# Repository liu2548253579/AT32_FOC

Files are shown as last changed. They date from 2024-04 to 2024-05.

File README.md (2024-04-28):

# AT32_FOC

## 介绍

此项目使用AT32主控驱动两路无刷电机，板载陀螺仪mpu6050，外置EEPROM，OLED屏幕，CAN口，两路AS5600磁编码器，旨在使用极低成本实现对无刷电机实现FOC控制，并且大部分元器件采用国产品牌，此板可用于无刷电机驱动，也可做为小平横车，预留串口和SWD调试接口方便后续外接其他设备。

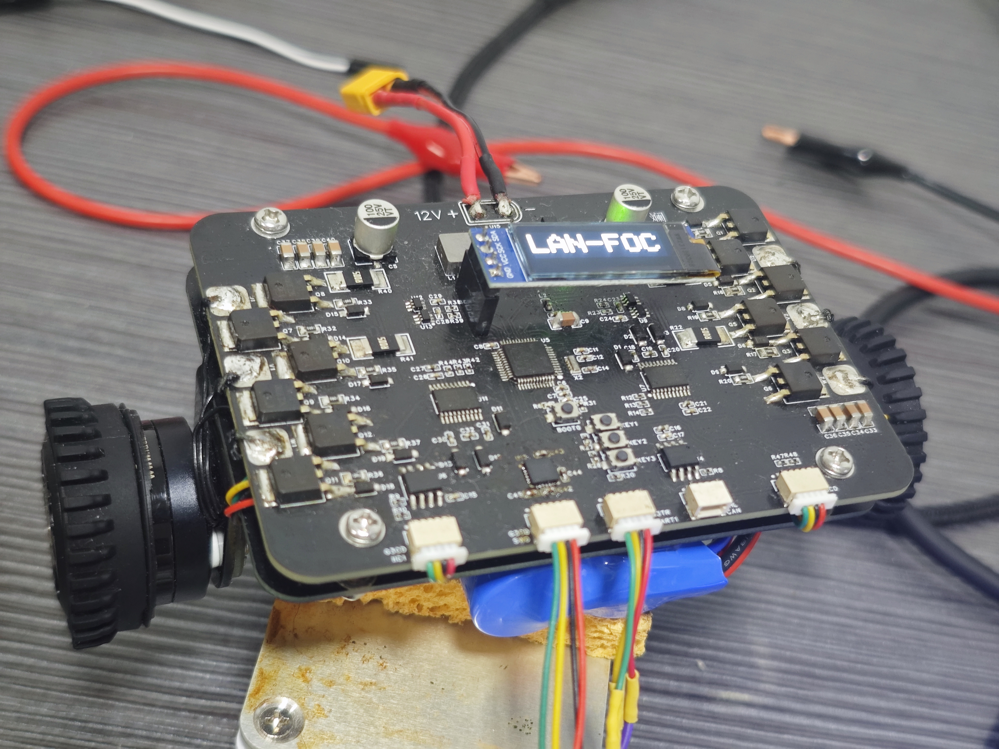
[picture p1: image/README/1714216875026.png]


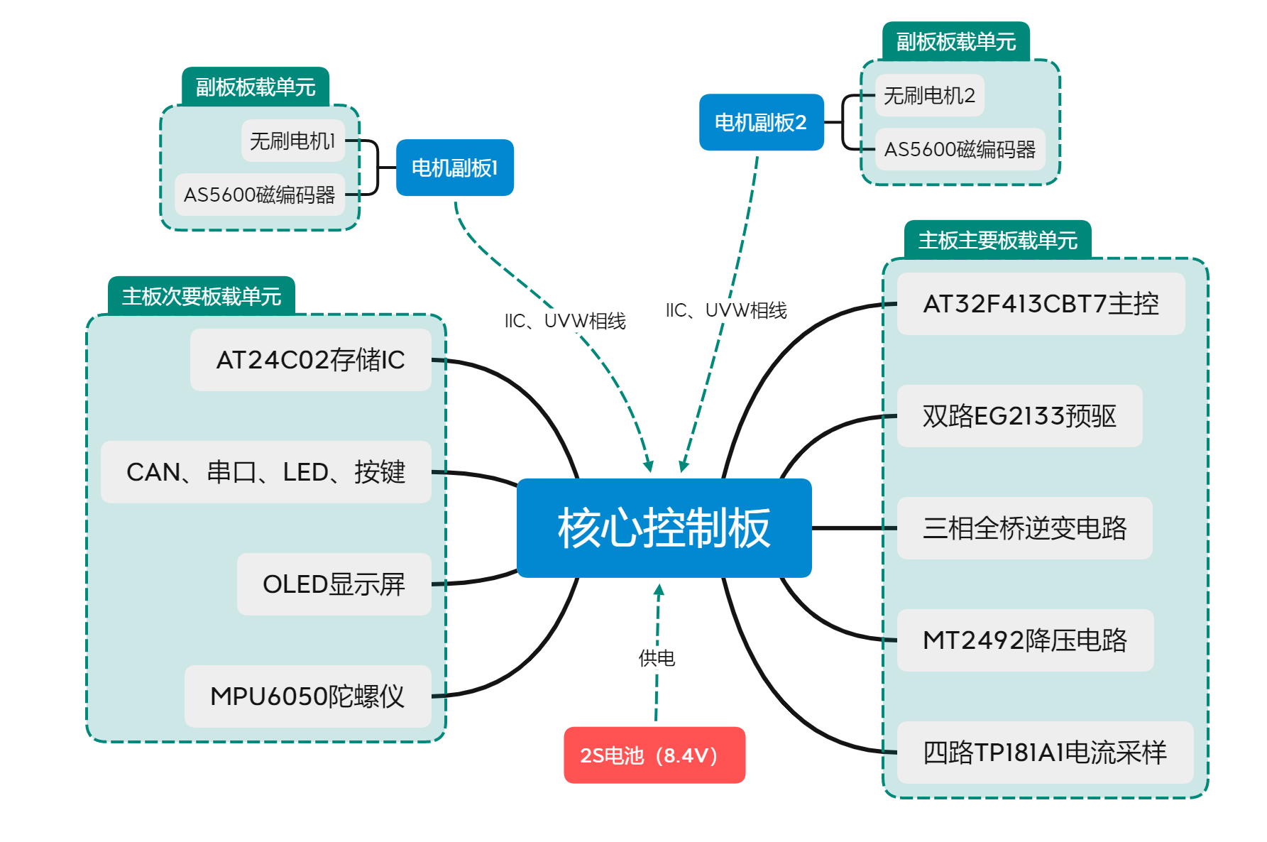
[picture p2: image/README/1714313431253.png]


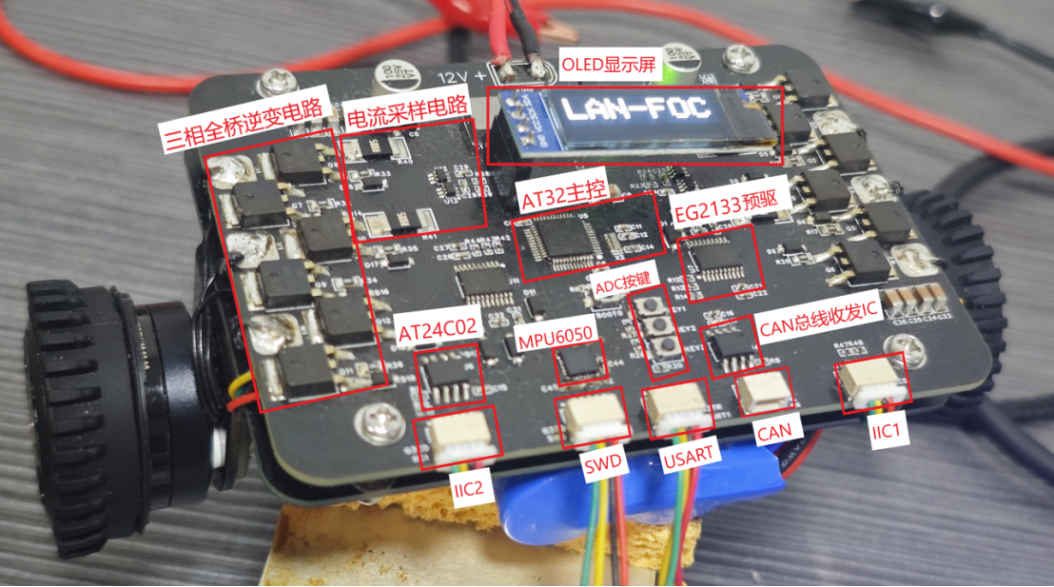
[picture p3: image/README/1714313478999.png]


## 一、硬件设置

请跟据hardware文件夹中的PCB文件打样PCB并将元器件贴装好，编码器底板适配带有径向磁铁的无刷电机

板子供电最大支持12V，但是我建议使用2S电池供电，也就是最大8.4V

无刷电机使用2210云台电机（110kV，6PP），但对于这个板子的MOS驱动能力来说完全是吕布骑狗了

预驱使用EG2133非常便宜，MOS使用NCE3080K足以应对绝大部分无刷电机

电流采样电阻为5毫欧的合金采样电阻，使用TP181A1-CR作为电流检测IC增益为50

MCU使用AT32F413CBT7

## 二、软件配置

软件使用platformio开发stm32程序基于Arduino框架，套用st官方维护的SDK，但是由于AT32和STM32的寄存器地址有部分不同，所以官方的SDK被我魔改过，在打开软件工程等待Platformio配置好环境之后，将此压缩包解压到你的platformio的package目录，这样我的修改就会生效，或者你如果不嫌麻烦或者想使用其他版本的SDK，可以根据我这两篇文章来自行配置：

[Arduino如何添加没有适配的GPIO](https://zhuanlan.zhihu.com/p/693456340)

[Arduino如何设置未适配的IO作为功能引脚](https://zhuanlan.zhihu.com/p/693467202)

在一切配置完毕之后你就可以烧录使用了，但注意我在ini配置中制定了烧录器为jlink如果你没有jlink请修改为其他方式

## 三、待完成事项

* [X] 完成AT32时钟适配
* [X] 完成ADC、PWM、UART、IIC、LED、KEY配置
* [X] 完成MPU6050、OLED、EEPROM、CAN配置
* [X] 实现无刷电机开环控制
* [X] 实现无刷电机角度闭环与速度闭环控制
* [X] 为无刷电机添加电流环
* [ ] 添加几个电机互动小功能
* [ ] 设计电池电压检测保护电池
* [ ] 设计多功能菜单调节参数
* [ ] 设计CAN协议实现参数在线查看与配置
* [ ] 调节PID使其可以直立并控制

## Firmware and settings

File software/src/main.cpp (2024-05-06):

#include "at32_config.h"
#include "foc_config.h"
#include "peripherals_config.h"
#include "menu.h"
#include "motion.h"
#include "interrupt.h"

#define protect_voltage 6.7f



void setup() {
  at32_board_init(); //CLOCK IO UART IIC initialization
  peripherals_init();//MPU6050 SSD1306 AT24C02

  Menu_Show_3("LOW-VOL");
  Get_Initial_Voltage(&sensor_data,protect_voltage);//6.7V initial voltage
  // eeprom.update(0x80,0x02);
  // Serial.println("data------------------------------");
  // Serial.println(eeprom.read(0x80));
  // Serial.println("data------------------------------");

  Menu_Show_3("HOLD-ON");
  mpu6050.calcGyroOffsets(false);


  // I2C1_EV_IRQn
  Menu_Show_3("LAN-FOC");
  foc_init(sensor_data.Bat_val_init);        //FOC initialization

  // bool ret = CANInit(CAN_500KBPS, 2);  // CAN_RX mapped to PB8, CAN_TX mapped to PB9
  // if (!ret) while(true);

  Menu_Show_3("INIT-OK");
  Serial.printf("INIT_OK\r\n");

  timer_init();//定时器初始化
}


void FOC_Loop(bool enable)
{
  runFOC();
  if(enable)
  {
    switch (main_menu.mode)
    {
    case 1:
      Motion_Set_Velocity_Both(Rpm_to_Rad(main_menu.Velocity));
      break;
    case 2:
      Motion_Sync();
      break;
    case 3:
      Motion_Set_Angle_Both(Angle_to_Rad(main_menu.Angle));
      break;
    case 4:
      Close_Output();
      Clear_FOC_Data();
      break;
    case 5:
      Close_Output();
      Clear_FOC_Data();
      break;

    default:
      break;
    }


  }




}



void loop() {


    if(time_1ms>=1)
    {
      time_1ms=0;
      FOC_Loop(main_menu.Enable);
    }
    

    if(time_10ms>=10)//10ms执行一次
    {
      time_10ms=0;
      Get_Mpu6050_Data(&sensor_data);
      Get_Foc_Data(&sensor_data);
      if(main_menu.Enable)
      {
        if(main_menu.mode==0)//Banlance
        {
          float out0,out1,out_velocity,out_velocity1;

          out_velocity=Motion_Balance_Velocity(sensor_data.Velocity_val,0.0f);
          out_velocity1=Motion_Balance_Velocity(sensor_data.Velocity_val1,0.0f);          
          out0=Motion_Balance_Angle(&sensor_data,out_velocity);
          out1=Motion_Balance_Angle(&sensor_data,out_velocity1);

          Banlance_Set_Velocity(0,out0);
          Banlance_Set_Velocity(1,out1);  
        }
        else
        {
          Serial_Print_All_Data(&sensor_data);
        }

      }
    }

    if(time_200ms>=200)//200ms执行一次
    {
      time_200ms=0;
      Get_Analog_Data(&sensor_data);
      ShowMenu(&main_menu);
      digitalToggleFast(LED_PIN);

      if(!main_menu.Enable)
      {
        Clear_FOC_Data();
        Close_Output();
      }

      if(sensor_data.Bat_val<protect_voltage)//低电量关闭输出
      {
        main_menu.Enable=0;
        Menu_Show_3("LOW-VOL");//显示低电量
        Close_Output();
      }
      if(sensor_data.Key_val==3)//确定键
      {
        sensor_data.Key_val=0;
        main_menu.Enable=!main_menu.Enable;
      }


      if(!main_menu.Enable)//主界面菜单
      {
        if(sensor_data.Key_val==1){sensor_data.Key_val=0;main_menu.mode--;}
        if(sensor_data.Key_val==2){sensor_data.Key_val=0;main_menu.mode++;}
      }
      else//功能界面
      {
        if(main_menu.mode==1)
        {
          if(sensor_data.Key_val==1){sensor_data.Key_val=0;main_menu.Velocity+=50;}
          if(sensor_data.Key_val==2){sensor_data.Key_val=0;main_menu.Velocity-=50;}
          if(main_menu.Velocity<=-500){main_menu.Velocity=-500;}
          if(main_menu.Velocity>=500){main_menu.Velocity=500;}
        }
        if(main_menu.mode==3)
        {
          if(sensor_data.Key_val==1){sensor_data.Key_val=0;main_menu.Angle+=30;}
          if(sensor_data.Key_val==2){sensor_data.Key_val=0;main_menu.Angle-=30;}
        }
      }


    }
}

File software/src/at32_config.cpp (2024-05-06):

#include "at32_config.h"
#include "math.h"

/*
线阻15欧姆
波特率115200

LED(PB1)
按键ADC(PA0)
电池ADC(PB0)

MOTOR1(PA8 PA9 PA10)
AS5600_1(PF6-SCL PF7-SDA)Wire1
I-SENSE1(PA6 PA7)

MOTOR2(PA1 PA2 PA3)
AS5600_2(PB10-SCL PB11-SDA)Wire
I-SENSE2(PA4 PA5)

MPU6050(PF6-SCL PF7-SDA)Wire1
FLASH(PF6-SCL PF7-SDA)Wire1
OLED(PB10-SCL PB11-SDA)Wire

SWD(PA13-CLK PA14-DIO)
USART1(PB6-TX PB7-RX)
CAN(PB8-RX PB9-TX)
*/

TwoWire Wire1 = TwoWire(); //D14-D15



void at32_i2c_clock_config(void)
{
__HAL_RCC_I2C1_CLK_ENABLE();
__HAL_RCC_AFIO_CLK_ENABLE();
__HAL_RCC_I2C1_REMAP_CLK_ENABLE();
__HAL_RCC_GPIOF_CLK_ENABLE();
}



void gpio_pin_remap_config(uint32_t gpio_remap, confirm_state new_state)
{
    uint32_t reg_addr, remap_mask;
    uint8_t bit_offset, bit_num, bit_val;

    /* get register address, bit offset, bit number and remap value */
    reg_addr = IOMUX_BASE + (gpio_remap >> 24);
    bit_offset = (gpio_remap >> 16) & 0xFF;
    bit_num = (gpio_remap >> 8) & 0xFF;
    bit_val = gpio_remap & 0xFF;

    /* get remap mask value */
    remap_mask = 0xFFFFFFFF << (32 - bit_num - bit_offset);
    remap_mask = remap_mask >> (32 - bit_num - bit_offset);
    remap_mask = remap_mask >> bit_offset;
    remap_mask = remap_mask << bit_offset;

    /* clear remap value */
    *(uint32_t*)reg_addr &= ~remap_mask;

    if(new_state != FALSE)
    {
        /* set remap value */
        *(uint32_t*)reg_addr |= (uint32_t)(bit_val << bit_offset);
    }
}


void Foc_Pin_Init(void)
{
    pinMode(PA8,OUTPUT);pinMode(PA9,OUTPUT);pinMode(PA10,OUTPUT);//初始化电机一引脚
    pinMode(PA1,OUTPUT);pinMode(PA2,OUTPUT);pinMode(PA3,OUTPUT);//初始化电机二引脚
    digitalWrite(PA8, LOW);digitalWrite(PA9, LOW);digitalWrite(PA10, LOW);//关闭电机一防止MOS管短路
    digitalWrite(PA1, LOW);digitalWrite(PA2, LOW);digitalWrite(PA3, LOW);//关闭电机二防止MOS管短路
    pinMode(PA4,INPUT);pinMode(PA5,INPUT);//左边电机I-SENSE
    pinMode(PA6,INPUT);pinMode(PA7,INPUT);//右边电机I-SENSE
}




void at32_board_init(void)
{   
    at32_i2c_clock_config();
    gpio_pin_remap_config(I2C1_GMUX_0011,TRUE);
    
    Foc_Pin_Init();

    Wire.setClock(400000); //设置I2C时钟频率为400kHz
    Wire1.setClock(400000); //设置I2C时钟频率为400kHz
    Wire1.setSCL(PF6);Wire1.setSDA(PF7);Wire1.begin();//初始化I2C接口1
    Wire.setSCL(PB10);Wire.setSDA(PB11);Wire.begin();//初始化I2C接口2
    Serial.setRx(PB7);Serial.setTx(PB6);Serial.begin(115200);//初始化串口

    pinMode(BAT_PIN,INPUT);//电池电压测量
    pinMode(KEY_PIN,INPUT_PULLDOWN);//按键ADC
    analogReadResolution(12);//设置ADC读取精度为12位

    pinMode(LED_PIN,OUTPUT);//初始化LED引脚
    digitalWrite(LED_PIN,LOW);//LED亮
    


    Serial.println("AT32_Board Init OK!");
    Serial.printf("Serial_OK!BaudRate:115200\r\nKEY(PA0)LED(PB1)\r\nBATTERY(PB0)\r\nMOTOR1(PA8 PA9 PA10)\r\nMOTOR2(PA1 PA2 PA3)\r\nI-SENSE1(PA6 PA7)\r\nI-SENSE2(PA4 PA5)\r\nIIC1(PF6-SCL PF7-SDA)-MPU-FLASH\r\nIIC2(PB10-SCL PB11-SDA)-OLED\r\nSWD(PA13-CLK PA14-DIO)\r\nUSART1(PB6-TX PB7-RX)\r\nCAN(PB8-RX PB9-TX)\r\n");
}



float at32_battery_voltage_read(void)
{
    float bat_voltage;
    uint32_t adc_val;
    adc_val=analogRead(BAT_PIN);
    bat_voltage=((float)adc_val/4095)*3.3*10.1;
    return bat_voltage;
}
// *40.16815554




uint8_t KEY_Read(void)
{   
    const uint8_t err_val=10;
    uint8_t key_val=0;
    uint32_t adc_val;
    float key_voltage;
    adc_val=analogRead(KEY_PIN);
    key_voltage=((float)adc_val/4095)*3.3*100;

    if(fabs(key_voltage-247.5)<=err_val){
        key_val=1;
    }
    else if(fabs(key_voltage-165)<=err_val){
        key_val=2;
    }
    else if(fabs(key_voltage-82.5)<=err_val){
        key_val=3;
    }

    return key_val;
}


uint8_t KEY_Read_Debounce(void)
{
uint8_t temp;
static uint8_t key_val_pre=0;
uint8_t key_val=KEY_Read();

if(key_val)//按键按下
{
    temp=0;
}
{//按键松开
    if(key_val!=key_val_pre)//按键状态改变
    {
        temp=key_val_pre;
    }
}

key_val_pre=key_val;
return temp;
}

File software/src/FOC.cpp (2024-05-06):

#include <Arduino.h>
#include "FOC.h"
#include "AS5600.h"
#include "lowpass_filter.h"
#include "pid.h"
#include "InlineCurrent.h"  //引入在线电流检测

#define _constrain(amt, low, high) ((amt) < (low) ? (low) : ((amt) > (high) ? (high) : (amt)))
float voltage_power_supply;
// float Ualpha,Ubeta=0,Ua=0,Ub=0,Uc=0;
#define _PI 3.14159265359f
#define _2PI 6.28318530718f
#define _PI_2 1.57079632679f
#define _PI_3 1.0471975512f
#define _3PI_2 4.71238898038f

float S0_zero_electric_angle = 0;
float S1_zero_electric_angle = 0;
int M0_PP = 1, M0_DIR = 1;
int M1_PP = 1, M1_DIR = 1;

//低通滤波初始化
LowPassFilter M0_Vel_Flt = LowPassFilter(0.01);   // Tf = 10ms   //M0速度环
LowPassFilter M1_Vel_Flt = LowPassFilter(0.01);   // Tf = 10ms   //M0速度环
LowPassFilter M0_Curr_Flt = LowPassFilter(0.05);  // Tf = 5ms   //M0电流环
LowPassFilter M1_Curr_Flt = LowPassFilter(0.05);  // Tf = 5ms   //M0电流环
//PID
PIDController vel_loop_M0 = PIDController(2, 0, 0, 100000, voltage_power_supply / 2);
PIDController angle_loop_M0 = PIDController(2, 0, 0, 100000, 100);
PIDController current_loop_M0 = PIDController(1.2, 0, 0, 100000, 12.6);
PIDController vel_loop_M1 = PIDController(2, 0, 0, 100000, voltage_power_supply / 2);
PIDController angle_loop_M1 = PIDController(2, 0, 0, 100000, 100);
PIDController current_loop_M1 = PIDController(1.2, 0, 0, 100000, 12.6);



//AS5600
Sensor_AS5600 S0 = Sensor_AS5600(0);
Sensor_AS5600 S1 = Sensor_AS5600(1);


#define _SQRT3 1.73205080757f
#define _SQRT3_2 0.86602540378f
#define _1_SQRT3 0.57735026919f
#define _2_SQRT3 1.15470053838f

//初始化电流闭环
CurrSense CS_M0 = CurrSense(0);
CurrSense CS_M1 = CurrSense(1);



//=================PID 设置函数=================
//速度PID
void FOC_M0_SET_VEL_PID(float P, float I, float D, float ramp, float limit)  //M0角度环PID设置
{
  vel_loop_M0.P = P;
  vel_loop_M0.I = I;
  vel_loop_M0.D = D;
  vel_loop_M0.output_ramp = ramp;
  vel_loop_M0.limit = limit;
}
//角度PID
void FOC_M0_SET_ANGLE_PID(float P, float I, float D, float ramp, float limit)  //M0角度环PID设置
{
  angle_loop_M0.P = P;
  angle_loop_M0.I = I;
  angle_loop_M0.D = D;
  angle_loop_M0.output_ramp = ramp;
  angle_loop_M0.limit = limit;
}
void FOC_M0_SET_CURRENT_PID(float P, float I, float D, float ramp)  //M0电流环PID设置
{
  current_loop_M0.P = P;
  current_loop_M0.I = I;
  current_loop_M0.D = D;
  current_loop_M0.output_ramp = ramp;
}
void FOC_M1_SET_VEL_PID(float P, float I, float D, float ramp, float limit)  //M0角度环PID设置
{
  vel_loop_M1.P = P;
  vel_loop_M1.I = I;
  vel_loop_M1.D = D;
  vel_loop_M1.output_ramp = ramp;
  vel_loop_M1.limit = limit;
}
//角度PID
void FOC_M1_SET_ANGLE_PID(float P, float I, float D, float ramp, float limit)  //M0角度环PID设置
{
  angle_loop_M1.P = P;
  angle_loop_M1.I = I;
  angle_loop_M1.D = D;
  angle_loop_M1.output_ramp = ramp;
  angle_loop_M1.limit = limit;
}
void FOC_M1_SET_CURRENT_PID(float P, float I, float D, float ramp)  //M0电流环PID设置
{
  current_loop_M1.P = P;
  current_loop_M1.I = I;
  current_loop_M1.D = D;
  current_loop_M1.output_ramp = ramp;
}


//M0速度PID接口
float FOC_M0_VEL_PID(float error)  //M0速度环
{
  return vel_loop_M0(error);
}
//M0角度PID接口
float FOC_M0_ANGLE_PID(float error) {
  return angle_loop_M0(error);
}
float FOC_M1_VEL_PID(float error)  //M0速度环
{
  return vel_loop_M1(error);
}
//M0角度PID接口
float FOC_M1_ANGLE_PID(float error) {
  return angle_loop_M1(error);
}


//初始变量及函数定义
#define _constrain(amt, low, high) ((amt) < (low) ? (low) : ((amt) > (high) ? (high) : (amt)))
//宏定义实现的一个约束函数,用于限制一个值的范围。
//具体来说，该宏定义的名称为 _constrain，接受三个参数 amt、low 和 high，分别表示要限制的值、最小值和最大值。该宏定义的实现使用了三元运算符，根据 amt 是否小于 low 或大于 high，返回其中的最大或最小值，或者返回原值。
//换句话说，如果 amt 小于 low，则返回 low；如果 amt 大于 high，则返回 high；否则返回 amt。这样，_constrain(amt, low, high) 就会将 amt 约束在 [low, high] 的范围内。1


// 归一化角度到 [0,2PI]
float _normalizeAngle(float angle) {
  float a = fmod(angle, _2PI);  //取余运算可以用于归一化，列出特殊值例子算便知
  return a >= 0 ? a : (a + _2PI);
  //三目运算符。格式：condition ? expr1 : expr2
  //其中，condition 是要求值的条件表达式，如果条件成立，则返回 expr1 的值，否则返回 expr2 的值。可以将三目运算符视为 if-else 语句的简化形式。
  //fmod 函数的余数的符号与除数相同。因此，当 angle 的值为负数时，余数的符号将与 _2PI 的符号相反。也就是说，如果 angle 的值小于 0 且 _2PI 的值为正数，则 fmod(angle, _2PI) 的余数将为负数。
  //例如，当 angle 的值为 -PI/2，_2PI 的值为 2PI 时，fmod(angle, _2PI) 将返回一个负数。在这种情况下，可以通过将负数的余数加上 _2PI 来将角度归一化到 [0, 2PI] 的范围内，以确保角度的值始终为正数。
}


void Close_Output (void)
{
  M0_setPwm(0,0,0);
  M1_setPwm(0,0,0);
}


// 设置PWM到控制器输出
void M0_setPwm(float Ua, float Ub, float Uc) {
  // 限制上限
  Ua = _constrain(Ua, 0.0f, voltage_power_supply);
  Ub = _constrain(Ub, 0.0f, voltage_power_supply);
  Uc = _constrain(Uc, 0.0f, voltage_power_supply);
  // 计算占空比
  // 限制占空比从0到1
  float dc_a = _constrain(Ua / voltage_power_supply, 0.0f, 1.0f);
  float dc_b = _constrain(Ub / voltage_power_supply, 0.0f, 1.0f);
  float dc_c = _constrain(Uc / voltage_power_supply, 0.0f, 1.0f);

  //写入PWM到PWM 0 1 2 通道
  ledcWrite(M0_PWM_U, dc_a * PWM_MAX_VALUE);
  ledcWrite(M0_PWM_V, dc_b * PWM_MAX_VALUE);
  ledcWrite(M0_PWM_W, dc_c * PWM_MAX_VALUE);
}

void M1_setPwm(float Ua, float Ub, float Uc) {
  // 限制上限
  Ua = _constrain(Ua, 0.0f, voltage_power_supply);
  Ub = _constrain(Ub, 0.0f, voltage_power_supply);
  Uc = _constrain(Uc, 0.0f, voltage_power_supply);
  // 计算占空比
  // 限制占空比从0到1
  float dc_a = _constrain(Ua / voltage_power_supply, 0.0f, 1.0f);
  float dc_b = _constrain(Ub / voltage_power_supply, 0.0f, 1.0f);
  float dc_c = _constrain(Uc / voltage_power_supply, 0.0f, 1.0f);

  //写入PWM到PWM 0 1 2 通道
  ledcWrite(M1_PWM_U, dc_a * PWM_MAX_VALUE);
  ledcWrite(M1_PWM_V, dc_b * PWM_MAX_VALUE);
  ledcWrite(M1_PWM_W, dc_c * PWM_MAX_VALUE);
}

// void M0_setTorque(float Uq, float angle_el) {
//   Uq = _constrain(Uq, -(voltage_power_supply) / 2, (voltage_power_supply) / 2);
//   // Serial.printf("M0%f\n",Uq);
//   float Ud = 0;
//   angle_el = _normalizeAngle(angle_el);
//   // 帕克逆变换
//   float Ualpha = -Uq * sinf(angle_el);
//   float Ubeta = Uq * cosf(angle_el);

//   // 克拉克逆变换
//   float Ua = Ualpha + voltage_power_supply / 2;
//   float Ub = (sqrt(3) * Ubeta - Ualpha) / 2 + voltage_power_supply / 2;
//   float Uc = (-Ualpha - sqrt(3) * Ubeta) / 2 + voltage_power_supply / 2;
//   M0_setPwm(Ua, Ub, Uc);
// }

// void M1_setTorque(float Uq, float angle_el) {
//   Uq = _constrain(Uq, -(voltage_power_supply) / 2, (voltage_power_supply) / 2);
//   // Serial.printf("M1%f\n",Uq);
//   float Ud = 0;
//   angle_el = _normalizeAngle(angle_el);
//   // 帕克逆变换
//   float Ualpha = -Uq * sinf(angle_el);
//   float Ubeta = Uq * cosf(angle_el);

//   // 克拉克逆变换
//   float Ua = Ualpha + voltage_power_supply / 2;
//   float Ub = (sqrt(3) * Ubeta - Ualpha) / 2 + voltage_power_supply / 2;
//   float Uc = (-Ualpha - sqrt(3) * Ubeta) / 2 + voltage_power_supply / 2;
//   M1_setPwm(Ua, Ub, Uc);
// }
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

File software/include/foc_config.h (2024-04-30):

#ifndef __FOC_CONFIG_H
#define __FOC_CONFIG_H

#include "at32_config.h"
#include "FOC.h"

#define FOC_PWM_FREQ 35000  //PWM频率
#define Resolution_PWM 10  //精度
#define PWM_MAX_VALUE 1023  //PWM最大值

#define M0_PWM_U PA_8
#define M0_PWM_V PA_9
#define M0_PWM_W PA_10

#define M1_PWM_U PA_1
#define M1_PWM_V PA_2
#define M1_PWM_W PA_3

#define M0_ADC_A PA_4
#define M0_ADC_B PA_5

#define M1_ADC_A PA_6
#define M1_ADC_B PA_7



//FOC算法参数设置
void foc_init(float power_supply);
void ledcWrite (uint32_t ulPin, uint32_t ulValue);


#endif /* __FOC_CONFIG_H */

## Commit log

2024-04-27 init repo
    [1_AS5600.schdoc.schdoc, 1_AT32_FOC_CORE.schdoc.schdoc, AS5600.pcbdoc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]
2024-04-28 add:photo of framework
2024-05-02 fix:pid param
